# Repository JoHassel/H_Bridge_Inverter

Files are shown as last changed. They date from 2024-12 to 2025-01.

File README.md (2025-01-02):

# H-Bridge Inverter 

## Goal
Basic functionality of an H-Bridge Inverter (12V DC --> 230V AC)

## Overview
1. Microcontroller (Raspi Pico) generates a sine PWM as a control signal
2. Sine PWM goes into a gate driver (Bootstrap) 
3. Bootstrap (one for each side) controls H-Bridge MOSFETs --> sine_wave AC

<br>

 <figure>
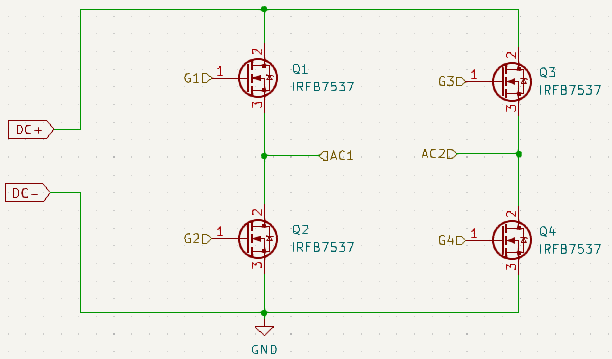
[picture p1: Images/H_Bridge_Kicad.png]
  
  <figcaption>Fig.1 - Simple H-Bridge </figcaption>
</figure> 

<br>

## Code
* based on [sPWM_Basic/sPWM_Basic.ino](https://github.com/Irev-Dev/Arduino-Atmel-sPWM/blob/d9c89ceef080a3c18ce5a02e0e310f1f46b8f579/sPWM_Basic/sPWM_Basic.ino)

### Flowchart
 <figure>
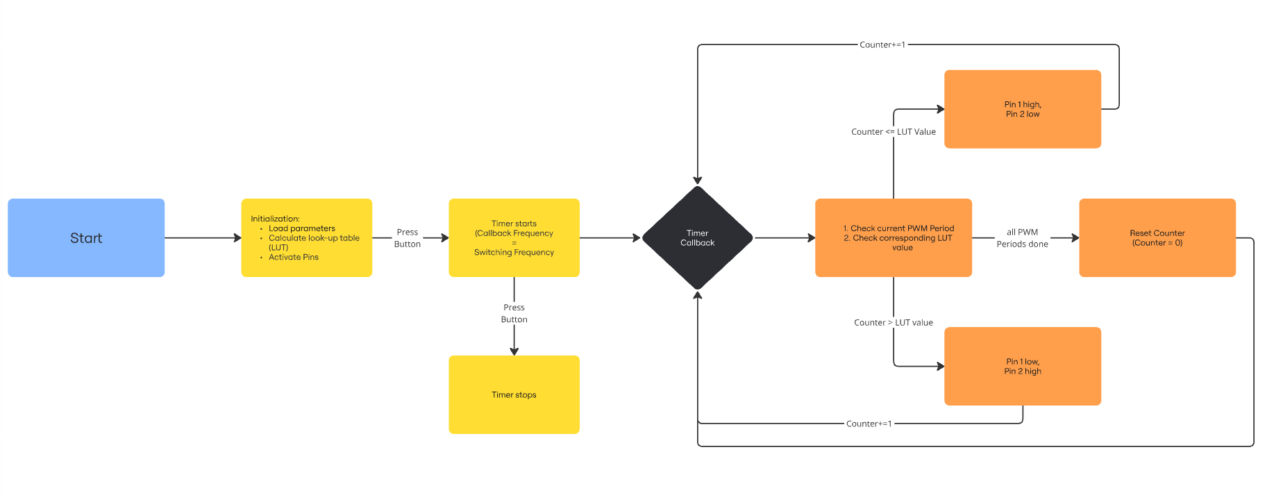
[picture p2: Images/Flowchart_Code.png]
  
  <figcaption>Fig.2 - Flowchart Code </figcaption>
</figure> 

<br>

### Output

 <figure>
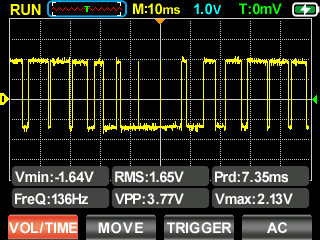
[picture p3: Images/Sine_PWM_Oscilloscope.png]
  
  <figcaption>Fig.3 - Sine PWM Output </figcaption>
</figure> 

<br>

## Hardware

### Why Bootstrap Circuit?
* source of high side MOSFET floats between V_AC (here: 12V AC) --> V_GS at the high side MOSFET must be high enough to safely switch on/off the MOSFET
* if low side MOSFET on, Bootstrap capacitor is chraged up to V_DC (here: 12V DC, voltage drop over bootstrap diode negligible)
* if high side MOSFET is switched on, the capacitor delivers its voltage to the control pin of the high side MOSFET

<br>

 <figure>
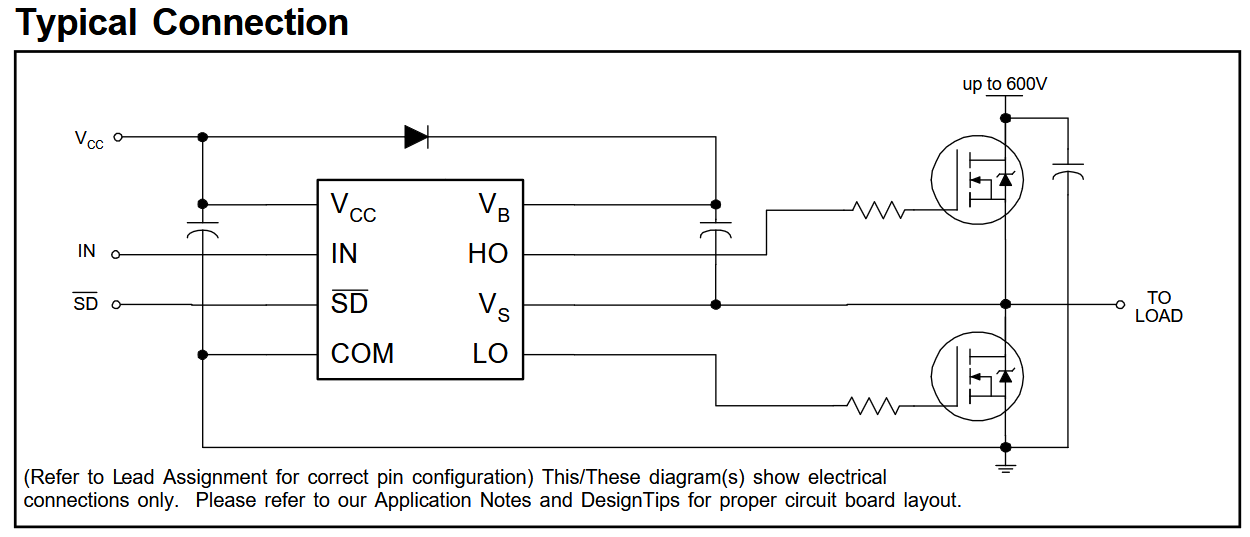
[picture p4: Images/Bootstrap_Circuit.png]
  
  <figcaption>Fig.4 - Bootstrap CIrcuit </figcaption>
</figure> 

<br>

### Circuit Design
* [Infineon IR2104](https://www.infineon.com/cms/de/product/power/gate-driver-ics/ir2104/) was used
* Dimensioning based on [TI Application Note](https://www.ti.com/lit/an/slua887a/slua887a.pdf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)
* MOSFETs: [IRFB7537](https://www.infineon.com/dgdl/Infineon-Data_Sheet_IRFS7537PBF-DS-v01_01-EN.pdf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)

#### Bootstrap Capacitor
$C_{boot} >= \frac{Q_{total}}{\Delta V_{HB}} = 183.75nF$  (Rule of thumb: 10 times gate capacitance leads to $190nF$) --> $C_{boot} = 200 nF$ 

$Q_{total} = Q_G + I_{HBS} \cdot \frac{D_{max}}{f_{sw}} + \frac{I_{HB}}{f_{sw}} $

* $Q_G = 210nC$ from [Data Sheet MOSFET](https://www.infineon.com/dgdl/Infineon-Data_Sheet_IRFS7537PBF-DS-v01_01-EN.pdf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)

* $I_{HBS} = 50 \mu A$ from [Data Sheet Gate Driver](https://www.infineon.com/cms/de/product/power/gate-driver-ics/ir2104/)

* $D_{max} = 1$ (will be slightly lower beacause of 520ns Dead time, 100% assumed for conservative caluclation)

* $f_{sw} = 10kHz$

* $I_ {HB} = 55 \mu A$ from [Data Sheet Gate Driver](https://www.infineon.com/cms/de/product/power/gate-driver-ics/ir2104/)

$\Delta V_{HB} = V_ {DD} − V_ {DH} − V_ {HBL} = 1.2V $

* $V_ {DD} = V_{DC} = 12V$

* $V_ {DH} = 1V $ from [Data Sheet 1N4148](https://www.vishay.com/docs/81857/1n4148.pdf)

* $V_{HBL} = 9.8V$ from [Data Sheet Gate Driver](https://www.infineon.com/cms/de/product/power/gate-driver-ics/ir2104/)

##### Bootstrap Resistor
$R_{boot} = \frac{V_{DD} - V_{Boot,Diode}}{I_{peak}} = 5.5 \Omega$ --> $5.6 \Omega$

* $V_{DD} = V_{DC} = 12V$

* $V_{Boot,Diode} = V_ {DH} = 1V $ from [Data Sheet 1N4148](https://www.vishay.com/docs/81857/1n4148.pdf)

* I_{peak} = I_{FSM} = 2A from [Data Sheet 1N4148](https://www.vishay.com/docs/81857/1n4148.pdf)

#### Gate Resistors
$R_{G,HS} = \frac{V_{Gate}}{I_{o+}} = 92 \Omega$ --> $91 \Omega$
* $V_{Gate} = V_{DC} = 12V$
* $I_{o+} >= 130mA $ from [Data Sheet Gate Driver](https://www.infineon.com/cms/de/product/power/gate-driver-ics/ir2104/)

$R_{G,LS} = \frac{V_{Gate}}{I_{o-}} = 44 \Omega$ --> $47 \Omega$
* $V_{Gate} = V_{DC} = 12V$
* $I_{o+} >= 270mA $ from [Data Sheet Gate Driver](https://www.infineon.com/cms/de/product/power/gate-driver-ics/ir2104/)

### Output Filter
* second order passive lowpass filter (LC filter)
* Cutoff frequency $f_g = \frac{1}{2 \pi \cdot \sqrt{LC}}$ (see [ElectronicBase.net](https://electronicbase.net/de/tiefpass-berechnen/))
* Cap chosen based on availabilty in store: $C_{Filter} = 10 \mu F$ (use film cap, not a polarized one)
* $L_{Filter} = 100mH$ --> $f_g = 159.2Hz$

## Results
The higher the resolution of the sine PWM (pwm_periods & scaler, see code) the clearer the sine wave output gets. Since the performance of the C code is better than the Micropython code (see below), the sine wave from the C code has less ripples. The amplitude is relatively low at the moment since there is no output voltage regulation yet. 

 <figure>
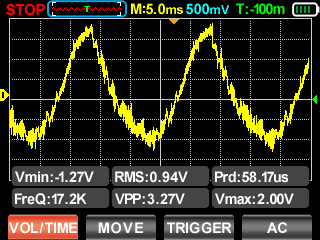
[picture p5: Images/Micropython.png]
  
  <figcaption>Fig.5 -Resulting Sine Wave with Micropython Code </figcaption>
</figure> 

<br>
<br>
<br>

<figure>
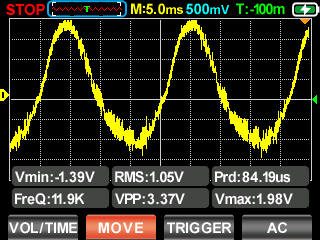
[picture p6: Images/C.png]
  
  <figcaption>Fig.6 -Resulting Sine Wave with C Code </figcaption>
</figure> 
<br>

## Performance
Disclaimer: I know Micropython is not made for high performance applications, but rather for rapid prototyping and easy debugging. I still wanted to see how far I can get with Micropython and compare it to C. 
Also the C code can become much faster by shorten the timer callback, using bit operations and more. 
I am looking forward to any improvement suggestions :)

| Language |	Code Version | 	$f_{sin,set}$ in Hz | $f_{sin,real}$ in Hz |	$f_{switch,real}$ in kHz |
| --- | --- | --- | --- | --- |
| MicroPython	| 26/12/2024	| 50	| 50	| 5 |  
| MicroPython	| 26/12/2024	| 100	| 100	| 10 |
| MicroPython	| 26/12/2024	| 500	| 105.3	| 10.5 |
| C	| 02/01/2025	| 50	| 50	| 5 |
| C	| 02/01/2025	| 100	| 100	| 10 |
| C	| 02/01/2025	| 500	| 444.4	| 44.4 |

## ToDos
* shorten timer callback 
* add output voltage regulation
* (if inductive load: add external flyback diodes in parallel to MOSFETs)

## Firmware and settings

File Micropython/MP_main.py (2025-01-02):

# Load libraries:
from machine import Pin
from math import sin, pi
from machine import Timer

# Initialize:
f_sine = 50                                     # Frequency of the generated sine wave
pwm_periods = 12                               # PWM Periods per half-wave
f_pwm = int(pwm_periods*f_sine)                 # PWM frequency
scaler = 12                                     # ratio between f_pwm and f_switch
f_switch = scaler * pwm_periods * f_sine *2     # Switching frequency
cycles = 0                                      # iterated on every timer callback
fin = scaler * pwm_periods * 2                  # cycle number at the end of a sine wave

# Calculate Look-up table:
r = range(1,pwm_periods+1)
sinewave = sin
lut = [int((scaler + (scaler*sin(2*pi*x/pwm_periods)))/2) for x in r]
# print(lut)

# Activate pins: 
g1 = Pin(16, Pin.OUT)
g2 = Pin(17, Pin.OUT)

# Timer Callback:
def clock_cb(timer):
    global cycles
    num = cycles % scaler                   # cycle number within a PWM period
    
    if num == 0:
        if cycles == fin:
            cycles = 0        
        g1.high()
        g2.low()
        # print("Pins 1&4 HIGH, Pins 2&3 LOW")

    i = int(cycles / (scaler * 2))      # number of PWM period
    if num == (lut[i]):
        g1.low()
        g2.high()
        # print("Pins 1&4 LOW, Pins 2&3 HIGH")
    
    cycles +=1
    # print(f"Callback, Cycle: {cycles}, Num: {num}, i: {i} Lut[i]: {lut[i]}")
    

# Timer Initialization:
tim_clock = Timer()
tim_clock.init(freq=f_switch, mode=Timer.PERIODIC, callback=clock_cb)

# Main loop:
while True:
    try:
        running = True
    except KeyboardInterrupt:
        running = False
        tim_clock.deinit()
        break

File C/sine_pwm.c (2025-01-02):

#include <stdio.h>
#include "pico/stdlib.h"
#include "hardware/timer.h"
#include "hardware/clocks.h"
#define _USE_MATH_DEFINES
#include <math.h>

#define HI 1
#define LO 0
#define g1 16          // GPIO for Gate 1
#define g2 17          // GPIO for Gate 2
#define f_sine 50      // Frequency of the generated sine wave
#define pwm_periods 20 // PWM Periods per half-wave
#define scaler 20      // ratio between f_pwm and f_switch

// Global Variables:
const int f_switch = pwm_periods * f_sine * scaler * 2; // Switching frequency
const int T_switch = (int)(1000000 / f_switch);         // Timer period in us
int cycles = 0;                                         // iterated on every timer callback
const int fin = scaler * pwm_periods * 2;               // cycle number at the end of a sine wave
int lut[pwm_periods];                                   // Look-up table for sine PWM

// Timer Callback
bool repeating_timer_callback(__unused struct repeating_timer *t)
{
    int num = cycles % scaler; // cycle number within a PWM period

    if (num == 0)
    {
        if (cycles == fin)
        {
            cycles = 0;
        }
        gpio_put(g1, HI);
        gpio_put(g2, LO);
        // printf("Gate 1&4 HIGH, Gate 2&3 LOW\n");
    }

    int i = (int)(cycles / (scaler * 2)); // number of PWM period
    if (num == (lut[i]))
    {
        gpio_put(g2, HI);
        gpio_put(g1, LO);
        // printf("Gate 1&4 LOW, Gate 2&3 HIGH\n");
    }

    cycles += 1;
    // printf("Callback, Cycle: %i, Num: %i, i: %i Lut[i]: %i\n", cycles, num, i, lut[i]);

    return true;
}

// GPIO initialisation:
int pins_init(void)
{
    gpio_init(g1);
    gpio_set_dir(g1, GPIO_OUT);
    gpio_init(g2);
    gpio_set_dir(g2, GPIO_OUT);
    return PICO_OK;
}

int main()
{
    stdio_init_all();
    pins_init();

    // Calculate Look-up table:
    for (int r = 1; r <= pwm_periods; r++)
    {
        lut[r - 1] = (int)((scaler + (scaler * sin(2 * M_PI * r / pwm_periods))) / 2);
        // printf("lut[%d] = %d\n", r, lut[r - 1]);
    }

    // Timer Initialization:
    struct repeating_timer timer;
    add_repeating_timer_us(T_switch, repeating_timer_callback, NULL, &timer);

    // Infinte Loop:
    while (true)
    {
        tight_loop_contents();
    }
}

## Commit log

2024-12-26 Update and rename pwm_basic.py to basic_PWM
2025-01-01 Add C Code
    [raspberrypi-swd.cfg]
2025-01-01 Restructuring Repo
    [raspberrypi-swd.cfg]
